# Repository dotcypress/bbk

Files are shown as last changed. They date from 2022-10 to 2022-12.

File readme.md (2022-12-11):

# bbk

🚜 Tiny printable robot platform

## License

Licensed under either of

- Apache License, Version 2.0 ([LICENSE-APACHE](LICENSE-APACHE) or
  http://www.apache.org/licenses/LICENSE-2.0)
- MIT license ([LICENSE-MIT](LICENSE-MIT) or http://opensource.org/licenses/MIT)

at your option.

### Contribution

Unless you explicitly state otherwise, any contribution intentionally submitted
for inclusion in the work by you, as defined in the Apache-2.0 license, shall be
dual licensed as above, without any additional terms or conditions.

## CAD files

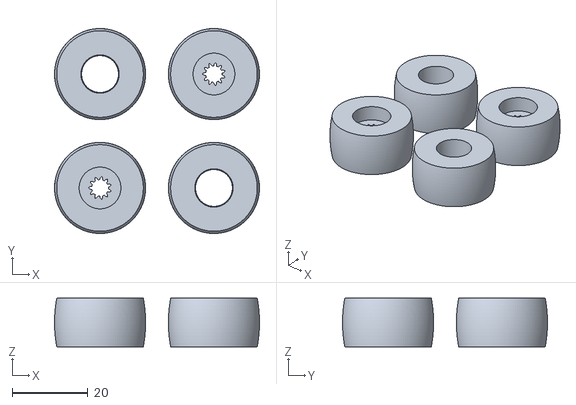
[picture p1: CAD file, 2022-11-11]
cad/bbk_wheels.stl
54.0 x 54.0 x 12.8

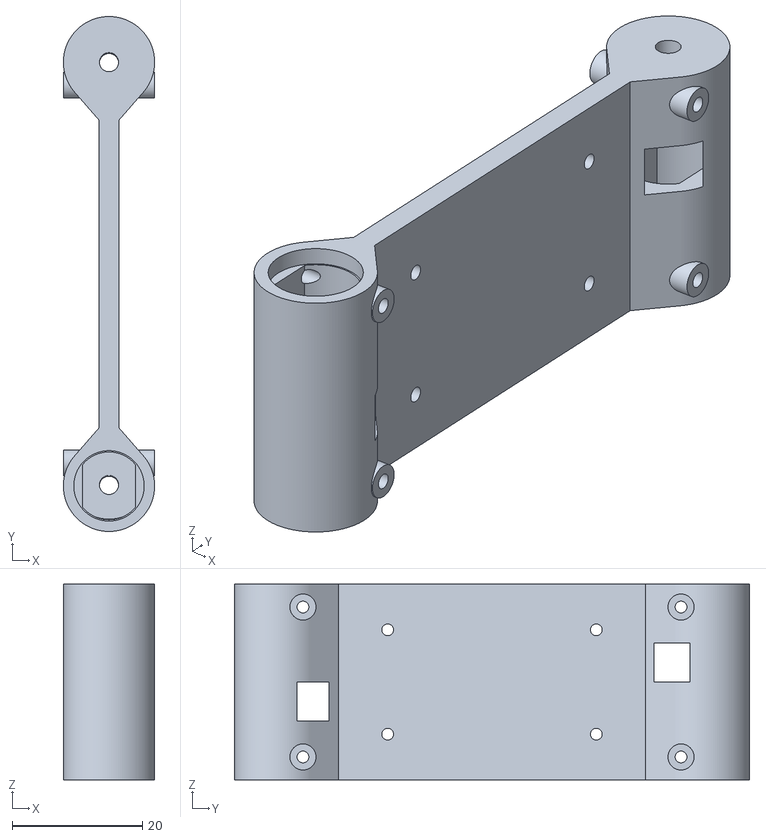
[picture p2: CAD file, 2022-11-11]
cad/bbk_frame.stl
14.0 x 79.0 x 30.0

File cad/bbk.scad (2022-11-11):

include <lib/9161c.scad>;

epsilon = 0.01;
base_height = 14;
base_width = 30;
base_length = 65;
bearing_r = 4.95;
m3_r = 1.47;
m2_r = 0.9;

module motors() {
  translate([base_width/2+5, base_length/2, 0])
    rotate([0, -90, 0]) 
    Motor9161c();

  translate([-base_width/2-5, -base_length/2, 0])
    rotate([0, 90, 0]) 
    Motor9161c();
}

module frame() {
  difference() {
    union() {
      translate([0, 0, 0])
        cube([base_width-epsilon, base_length, 3], center=true);

      hull() {
        translate([0, -base_length/2+9, 0])
          cube([base_width-epsilon, 1, 2], center=true);
        translate([0, -base_length/2, 0])
          rotate([0, 90, 0]) 
          cylinder(r=base_height/2, h=base_width-epsilon, center=true);
      }

      hull() {
        translate([0, base_length/2-9, 0])
          cube([base_width-epsilon, 1, 2], center=true);
        translate([0, base_length/2, 0])
          rotate([0, 90, 0]) 
          cylinder(r=base_height/2, h=base_width-epsilon, center=true);
      }

      translate([11.5, 29, 0]) 
        cylinder(r=2, h=base_height, center=true);
      translate([-11.5, 29, 0]) 
        cylinder(r=2, h=base_height, center=true);
      translate([11.5, -29, 0]) 
        cylinder(r=2, h=base_height, center=true);
      translate([-11.5, -29, 0]) 
        cylinder(r=2, h=base_height, center=true);
    }

    union() {
      motors();

      translate([base_width/2, -base_length/2, 0])
        rotate([0, 90, -1]) 
        cylinder(r=m3_r, h=base_width, center=true);
      translate([-base_width/2, base_length/2, 0])
        rotate([0, 90, -1]) 
        cylinder(r=m3_r, h=base_width, center=true);

      translate([3, -base_length/2+1.5, 0])
        rotate([0, 90, 0]) 
        cylinder(r=base_height/2-0.4, h=6, center=true);
      translate([-3, base_length/2-1.5, 0])
        rotate([0, 90, 0]) 
        cylinder(r=base_height/2-0.3, h=6, center=true);

      union() {
        translate([8, -16, 0]) 
          cylinder(r=m2_r, h=10, center=true);
        translate([-8, -16, 0]) 
          cylinder(r=m2_r, h=10, center=true);
        translate([8, 16, 0]) 
          cylinder(r=m2_r, h=10, center=true);
        translate([-8, 16, 0]) 
          cylinder(r=m2_r, h=10, center=true);

        translate([11.5, 29, 0]) 
          cylinder(r=m2_r, h=20, center=true);
        translate([-11.5, 29, 0]) 
          cylinder(r=m2_r, h=20, center=true);
        translate([11.5, -29, 0]) 
          cylinder(r=m2_r, h=20, center=true);
        translate([-11.5, -29, 0]) 
          cylinder(r=m2_r, h=20, center=true);
      }
    }
  }
}

module wheel(inner_r=bearing_r) {
  outer_r=12;
  width=12.8;
  intersection() {
    difference() {
      cylinder(r=outer_r, h=width, center=true);

      translate([0, 0, width/4])
        cylinder(r1=inner_r-0.1, r2=inner_r+0.1, h=width/2+epsilon, center=true);
      translate([0, 0, -width/4])
        cylinder(r1=inner_r+0.1, r2=inner_r-0.1, h=width/2+epsilon, center=true);
   
    }
    scale([1, 1, 1.7])
      sphere(r=outer_r);
  }
}

module motor_wheel() {
  translate([0, 0, 2]) 
    Motor9161cCoupler(height=4, rim_width=4);
  difference() {
    wheel();
    translate([0,0,4]) 
      cylinder(r=5.5, h=10, center=true);
  }
}

module demo() {
  $fn=32;

  %motors();
  frame();
  union() {
    translate([base_width/2+8, base_length/2, 0]) 
      rotate([0, 90, 0])
      motor_wheel();
    translate([base_width/2+8, -base_length/2, 0]) 
      rotate([0, -90, 0])
      wheel();

    translate([-base_width/2-8, base_length/2, 0]) 
      rotate([0, 90, 0])
      wheel();
    translate([-base_width/2-8, -base_length/2, 0]) 
      rotate([0, -90, 0])
      motor_wheel();
  }
}

module wheels_print() {
  $fn=128;
  translate([15, 15, 6.4])
    motor_wheel();
  translate([15, -15, 6.4])
    wheel();

  translate([-15, 15, 6.4])
    wheel();
  translate([-15, -15, 6.4])
    motor_wheel();
}

module frame_print() {
  $fn=128;
  translate([0, 0, base_width/2])
    rotate([0, 90, 0])
    frame();
}

*wheels_print();
*frame_print();
demo();

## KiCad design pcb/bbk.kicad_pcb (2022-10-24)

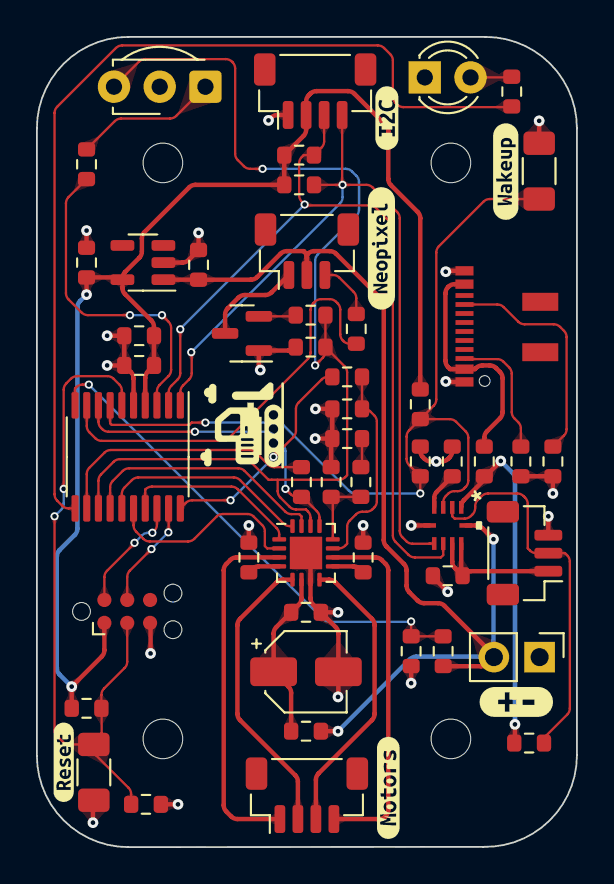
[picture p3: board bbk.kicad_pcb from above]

Board: 4 copper layers, 30.0 x 45.0 mm, 60 parts (0 on the bottom side), 43 nets.

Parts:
C1, C3, C4, C6, C8, C9: 10uF; R_0603_1608Metric
C2, C5, C7, C10: 100nF; R_0603_1608Metric
C11: 22uF; CP_Elec_4x4.5
C12: 22nF; R_0603_1608Metric
D1: TSAL4400; LED_D3.0mm_IRBlack
F1: Polyfuse; R_0603_1608Metric
FB1: FerriteBead; R_0603_1608Metric
H1, H2, H3, H4: MountingHole; MountingHole_2.2mm_M2
J1: USB_C_Receptacle_USB2.0; USB_C_Receptacle_JAE_DX07S016JA3R1500
J2: Neopixel; JST_SH_BM03B-SRSS-TB_1x03-1MP_P1.00mm_Vertical
J3: ExtPower; PinHeader_1x02_P2.54mm_Vertical
J4: TagConnect; Tag-Connect_TC2030-IDC-NL_2x03_P1.27mm_Vertical
J5: Li-Ion; JST_SH_BM03B-SRSS-TB_1x03-1MP_P1.00mm_Vertical
J6: I2C; JST_SH_BM04B-SRSS-TB_1x04-1MP_P1.00mm_Vertical
J7: Motors; JST_SH_BM04B-SRSS-TB_1x04-1MP_P1.00mm_Vertical
Q1: PMV15ENEA; SOT-23
R1, R6, R7, R9, R12, R20: 10K; R_0603_1608Metric
R2, R5, R10: 190R; R_0603_1608Metric
R3, R4, R13, R18, R19: 5.1K; R_0603_1608Metric
R8: 20K; R_0603_1608Metric
R11: 330R; R_0603_1608Metric
R14: 47K; R_0603_1608Metric
R15: 1K; R_0603_1608Metric
R16, R17: 2R; R_0603_1608Metric
SW1: Reset; R_1206_3216Metric_Pad1.30x1.75mm_HandSolder
SW2: Wakeup; R_1206_3216Metric_Pad1.30x1.75mm_HandSolder
U1: STM32G0xxFx; TSSOP-20_4.4x6.5mm_P0.65mm
U2: MP2667GG-xxxx-Z
U3: TSOP93338; Vishay_MINICAST-3Pin
U4: AP7370-33W5-7; TSOT-23-5
U5: STSPIN240; VQFN-16-1EP_3x3mm_P0.5mm_EP1.8x1.8mm
kibuzzard-6354BB14: G***; kibuzzard-6354BB14
kibuzzard-6354BBA3: G***; kibuzzard-6354BBA3
kibuzzard-6354BC68: G***; kibuzzard-6354BC68
kibuzzard-6354BC97: G***; kibuzzard-6354BC97
kibuzzard-6354BCC6: G***; kibuzzard-6354BCC6
kibuzzard-6354BCF7: G***; kibuzzard-6354BCF7

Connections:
+3.3V: C1.1, C2.1, C8.1, J4.1 (Vdd), J6.2, R6.1, R9.1, R18.2, R19.2, U1.4 (VDD), U4.5 (VOUT)
/ADC_BAT: R7.2, R8.1, U1.10 (PA3)
/BAT+: C4.2, J5.1, U2.8 (BATT), U2.9 (BATT)
/CHARGER_VDD: C3.2, U2.4 (VDD)
/CHARGER_VIN: F1.2, R20.2, U2.1 (IN)
/DRIVE_EN: R12.1, U1.12 (PA5)
/DRIVE_REF: R13.2, U1.20 (PB3/PB4/PB5/PB6)
/FAULT: R12.2, U1.8 (PA1), U5.13 (EN/FLT)
/I2C_INT: C7.1, R9.2, SW2.1, U1.7 (PA0), U2.3 (INT)
/I2C_SCL: J6.4, R19.1, U1.1 (PB7/PB8), U2.6 (SCL)
/I2C_SDA: J6.3, R18.1, U1.2 (PB9/PC14/OSC_IN), U2.7 (SDA)
/IR_RX: R10.1, U1.3 (PC15/OSC_OUT)
/IR_TX: R11.2, U1.11 (PA4)
/MOTOR_A1: J7.1, U5.3 (OUTA1)
/MOTOR_A2: J7.2, U5.5 (OUTA2)
/MOTOR_A_SENSE: R16.1, U5.4 (SENSEA)
/MOTOR_B1: J7.4, U5.10 (OUTB1)
/MOTOR_B2: J7.3, U5.8 (OUTB2)
/MOTOR_B_SENSE: R17.1, U5.9 (SENSEB)
/MOTOR_VSS: C10.1, C11.1, FB1.2, U5.6 (VS)
/NEOPIXEL: R5.2, U1.9 (PA2)
/NEOPIXEL_GND: J2.1, Q1.3 (D)
/NTC: J5.2, R20.1, U2.2 (NTC)
/PHASE_A: U1.17 (PA12[PA10]), U5.1 (PHA)
/PHASE_B: U1.14 (PA7), U5.15 (PHB)
/PWM_A: U1.16 (PA11[PA9]), U5.2 (PWMA)
/PWM_B: U1.15 (PB0/PB1/PB2/PA5), U5.16 (PWMB)
/STANDBY: R1.1, R2.2, U1.13 (PA6), U3.3 (Vs), U5.14 (STBY/RESET)
/V_USB: F1.1, J1.A4 (VBUS), J1.A9 (VBUS)
/nRST: C5.1, J4.3 (nRST), R6.2, SW1.1, U1.6 (NRST)
GND: C1.2, C2.2, C3.1, C4.1, C5.2, C6.2, C7.2, C8.2, C9.2, C10.2, C11.2, C12.2, D1.1 (K), J1.A1 (GND), J1.A12 (GND), J3.1, J4.5 (GND), J5.3, J6.1, Q1.1 (S), R1.2, R3.2, R4.2, R8.2, R15.1, R16.2, R17.2, SW1.2, SW2.2, U1.5 (VSS), U2.5 (GND), U3.2 (GND), U4.2 (GND), U5.7 (GND), U5.17 (EPAD)
unnamed: C12.1, R14.1
unnamed: D1.2 (A), R11.1
unnamed: J1.A5 (CC1), R3.1
unnamed: J1.B5 (CC2), R4.1
unnamed: J2.3, R5.1
unnamed: J4.4 (SWDCLK), U1.19 (PA14/PA15/BOOT)
unnamed: J4.2 (SWDIO), U1.18 (PA13)
unnamed: Q1.2 (G), R2.1
unnamed: R10.2, U3.1 (OUT)
unnamed: C9.1, R13.1, U5.11 (REF)
unnamed: R14.2, R15.2, U5.12 (TOFF)
VBUS: C6.1, FB1.1, J2.2, J3.2, R7.1, U2.10 (SYS), U4.1 (VIN)

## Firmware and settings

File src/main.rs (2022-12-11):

#![no_std]
#![no_main]
// #![deny(warnings)]

use defmt_rtt as _;
pub extern crate stm32g0xx_hal as hal;

extern crate panic_halt;
extern crate rtic;

mod esc;
mod ir;
mod pins;

use esc::*;
use hal::analog::adc;
use hal::gpio::SignalEdge;
use hal::i2c;
use hal::power::WakeUp;
use hal::prelude::*;
use hal::rcc::{self, PllConfig};
use hal::spi;
use hal::stm32;
use hal::stm32::*;
use ir::*;
use pins::*;
use smart_leds::*;
use ws2812_spi as ws2812;

#[rtic::app(device = stm32, peripherals = true)]
mod curio {
    use super::*;

    #[shared]
    struct Shared {
        ir: IrTransceiver,
        exti: EXTI,
        esc: MotorControl,
    }

    #[local]
    struct Local {}

    #[init]
    fn init(ctx: init::Context) -> (Shared, Local, init::Monotonics) {
        defmt::info!("init");
        // Configure APB bus clock to 48MHz, cause ws2812 requires 3Mbps SPI
        let pll_cfg = PllConfig::with_hsi(4, 24, 2);
        let rcc_cfg = rcc::Config::pll().pll_cfg(pll_cfg);
        let mut rcc = ctx.device.RCC.freeze(rcc_cfg);

        let pins = Pins::new(
            ctx.device.GPIOA,
            ctx.device.GPIOB,
            ctx.device.GPIOC,
            &mut rcc,
        );

        let mut exti = ctx.device.EXTI;
        let mut standby = pins.standby;
        let wakeup = pins.wakeup_button.listen(SignalEdge::Falling, &mut exti);

        let battery_sense = pins.battery_sense;
        let mut adc = ctx.device.ADC.constrain(&mut rcc);
        adc.set_sample_time(adc::SampleTime::T_80);
        adc.set_precision(adc::Precision::B_12);

        let mut ir_tim = ctx.device.TIM17.pwm(IR_TIMER_FREQUENCY.Hz(), &mut rcc);
        ir_tim.listen();

        let ir_carrier_tim = ctx.device.TIM14.pwm(IR_CARRIER_FREQUENCY.Hz(), &mut rcc);
        let rx = pins.ir_rx.listen(SignalEdge::All, &mut exti);
        let ir = IrTransceiver::new(ir_tim, ir_carrier_tim, pins.ir_tx, rx);

        let mut pwr = ctx.device.PWR.constrain(&mut rcc);
        pwr.clear_standby_flag();
        pwr.enable_wakeup_lane(WakeUp::Line1, SignalEdge::Falling);

        let i2c = ctx.device.I2C1.i2c(
            pins.i2c_sda,
            pins.i2c_clk,
            i2c::Config::new(400.kHz()),
            &mut rcc,
        );

        let spi = ctx.device.SPI1.spi(
            (spi::NoSck, spi::NoMiso, pins.neopixel),
            ws2812::MODE,
            3.MHz(),
            &mut rcc,
        );
        let mut neopixel = ws2812::Ws2812::new(spi);

        let mut data: [RGB<u8>; 10] = [RGB::default(); 10];
        for (idx, c) in data.iter_mut().enumerate() {
            *c = RGB {
                r: idx as _,
                g: 0,
                b: 0,
            };
        }
        neopixel.write(data.iter().cloned()).unwrap();

        standby.set_high().ok();
        let mut esc = MotorControl::new(
            ctx.device.TIM1,
            ctx.device.TIM16,
            pins.motor_driver_tork,
            pins.motor_driver_enable,
            pins.motor_driver_fault,
            pins.motor_a_pwm,
            pins.motor_b_pwm,
            pins.motor_a_phase,
            pins.motor_b_phase,
            &mut rcc,
        );

        esc.on();

        defmt::info!("init done");
        (Shared { ir, exti, esc }, Local {}, init::Monotonics())
    }

    #[task(binds = TIM1_BRK_UP_TRG_COM, shared = [esc])]
    fn esc_tick(ctx: esc_tick::Context) {
        let mut esc = ctx.shared.esc;
        esc.lock(|esc| esc.tick());
    }

    #[task(binds = EXTI0_1, shared = [exti])]
    fn wakeup(ctx: wakeup::Context) {
        let mut exti = ctx.shared.exti;
        exti.lock(|exti| exti.unpend(hal::exti::Event::GPIO0));
    }

    #[task(binds = TIM17, shared = [ir])]
    fn ir_timer_tick(ctx: ir_timer_tick::Context) {
        let mut ir = ctx.shared.ir;
        ir.lock(|ir| ir.tick());
    }

    #[task(binds = EXTI4_15, shared = [ir, exti, esc])]
    fn ir_rx(ctx: ir_rx::Context) {
        let mut exti = ctx.shared.exti;
        let mut ir = ctx.shared.ir;
        let mut esc = ctx.shared.esc;
        exti.lock(|exti| exti.unpend(hal::exti::Event::GPIO15));
        if let Ok(Some(cmd)) = ir.lock(|ir| ir.event()) {
            defmt::info!("ir: {}", cmd.cmd);
            let speed = match cmd.cmd {
                12 => 32,
                24 => 64,
                94 => 127,
                _ => 0,
            };
            esc.lock(|esc| esc.set_speed(speed, speed))
        }
    }
}

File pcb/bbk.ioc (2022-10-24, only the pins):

Mcu.UserName=STM32G030F6Px
PA0.GPIO_Label=I2C_INT
PA0.Signal=SYS_WKUP1
PA1.GPIO_Label=STBY
PA1.Signal=GPIO_Output
PA13.Signal=SYS_SWDIO
PA14-BOOT0.Signal=SYS_SWCLK
PA2.GPIO_Label=NEOPIXEL
PA2.Signal=SPI1_MOSI
PA3.GPIO_Label=ADC_BAT
PA3.Signal=ADC1_IN3
PA4.GPIO_Label=IR_TX
PA4.Signal=S_TIM14_CH1
PA5.GPIO_Label=MOTOR_EN
PA5.Signal=GPIO_Output
PA6.GPIO_Label=MOTOR_FAULT
PA6.Signal=GPIO_Output
PA7.GPIO_Label=PHASE_B
PA7.Signal=GPIO_Output
PA8.GPIO_Label=PWM_B
PA8.Signal=S_TIM1_CH1
PB6.GPIO_Label=MOTOR_REF
PB6.Signal=TIM16_CH1N
PB8.Signal=I2C1_SCL
PB9.Signal=I2C1_SDA

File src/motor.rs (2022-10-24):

#![allow(dead_code)]

use hal::rcc::Rcc;
use hal::timer::pwm::*;
use hal::timer::*;

use crate::*;

pub struct MotorControl {
    enable: MotorDriverEnable,
    fault: MotorDriverFault,
    tork: PwmPin<TIM16, Channel1>,
    pwm_a: PwmPin<TIM1, Channel4>,
    pwm_b: PwmPin<TIM1, Channel1>,
    phase_a: MotorAPhase,
    phase_b: MotorBPhase,
}

impl MotorControl {
    #[allow(clippy::too_many_arguments)]
    pub fn new(
        speed_tim: TIM1,
        tork_tim: TIM16,
        tork: MotorDriverTork,
        enable: MotorDriverEnable,
        fault: MotorDriverFault,
        pwm_a: MotorAPwm,
        pwm_b: MotorBPwm,
        phase_a: MotorAPhase,
        phase_b: MotorBPhase,
        rcc: &mut Rcc,
    ) -> Self {
        let tork_pwm = tork_tim.pwm(10.kHz(), rcc);
        let mut tork = tork_pwm.bind_pin(tork);
        tork.set_duty(tork.get_max_duty());
        tork.enable();

        let speed_pwm = speed_tim.pwm(100.Hz(), rcc);
        let mut pwm_a = speed_pwm.bind_pin(pwm_a);
        pwm_a.set_duty(0);
        pwm_a.enable();

        let mut pwm_b = speed_pwm.bind_pin(pwm_b);
        pwm_b.set_duty(0);
        pwm_b.enable();

        Self {
            tork,
            enable,
            fault,
            pwm_a,
            pwm_b,
            phase_a,
            phase_b,
        }
    }
}

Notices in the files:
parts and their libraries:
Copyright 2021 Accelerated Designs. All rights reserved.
